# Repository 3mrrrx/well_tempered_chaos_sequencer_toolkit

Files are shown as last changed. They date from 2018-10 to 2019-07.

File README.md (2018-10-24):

# introduction: 

the well-tempered chaos tool-kit is a mechanical chaos based musical system that seeks to create an intuitive musical relation to the underlying generic structures of chaos in systems. Chaos is generated by the paths of ball bearings that fall though a modular geometrical structure of pins. Depending on the path of a ball the sequencer triggers a sound events, such as CV, MIDI or OSC.

https://vimeo.com/296761849

By adding a mechanism to endlessly loop the balls over the pins the chaos can be continuously sampled. Through the repeated sampling of the chaos generated by a pin formation a structure can be recognized. In return the sequencer uses this structure to trigger sound events. By changing the geometrical patterns of the pins different sound event structures can be constructed that resemble or approximate musical patterns. 

When the ball loops infinitely the sequencer can become a musical object, that  autonomously expresses musical structures. The idea, that simulates randomness can converge through mechanical computation to different statistical distributions structures (Gaussian, non-Gaussian, Boltzmann etc.), is used to express well-tempered chaotic musical events. 

# how to run:

for creating the geometry:

1. download and install OpenSCAD
www.openscad.org/

2. run the script to create the STL models

for preparing the arudino:

1. download ans install the Arduino-IDE
https://www.arduino.cc/

# project

The full project description and build  instruction can be found on "hackaday.io" project:
https://hackaday.io/project/161589-the-well-tempered-chaos-sequencer

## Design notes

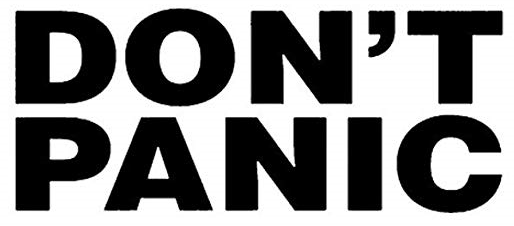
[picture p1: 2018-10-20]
simulation/case_1/dont_apnic.png

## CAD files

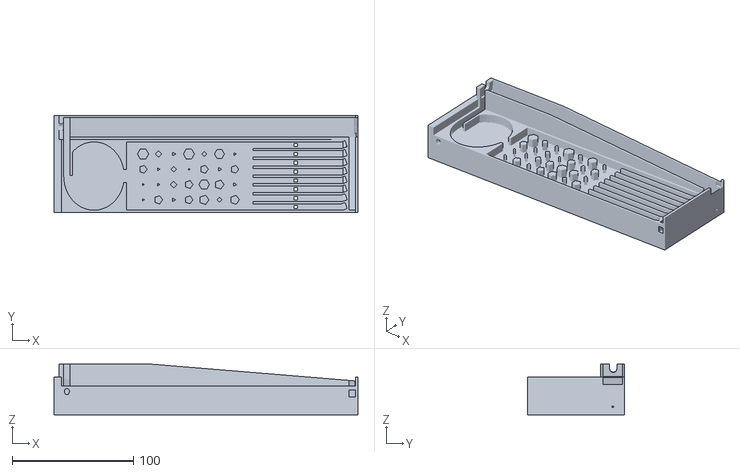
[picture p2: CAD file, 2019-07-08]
geometry/version_4/version4 _BETTER.stl
250.8 x 80.3 x 41.7

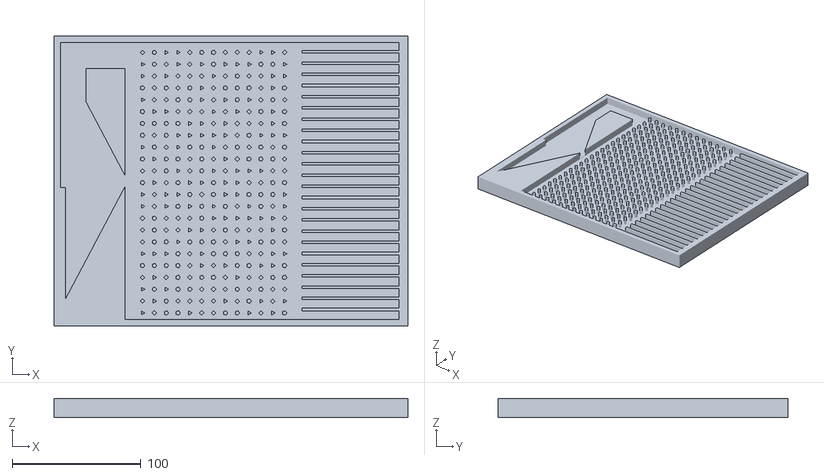
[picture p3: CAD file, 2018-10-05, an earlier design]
geometry/version_1/version_1.1.stl
275.0 x 225.0 x 15.0

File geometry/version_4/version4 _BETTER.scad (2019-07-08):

// well-tempered chaos sequencer board version 3.0
// 5/8/2018   By: 3mrrrx
// GNU GPLv3
// all values are in [mm]


////////////////////////////////////////////
// include functions
////////////////////////////////////////////

include <functions.scad>

////////////////////////////////////////////
// global variables
////////////////////////////////////////////

// tolerance plus ball raduis 
tol = 0.4; //0.24
Ball_raduis = 2.25 + tol;

//thinkness of each of the wall
wall_thinkness = 2 ;

// bottom floor thinknes goes in -z
floor_thinkess = 9.5 + 5;

// board dimenstion 
size_x = 235.55; //240-3.7-1+0.25;
size_y = 60.4;
size_z = Ball_raduis*3.5;

// bin size parameters
cascades_lengths = 115 * size_x/350;
spacing_factor = 1; // factor to multiply to bin width  

// bin end break paramter 
break_factor = 1;  // fraction of bin length 
break_angel  = 20; // angel of bread degs


// fann funnel parameters
funnel_size = 50 ; // lentgh of funnel
funnel_resulition = 50; // funnel cirular resolution
inlet_factor = 2;   // 
$fn = 10;

// fan dimensions
fan_x = 72;
fan_y = 40;
fan_z = 40;
factor_fan = 0.5; // position of fan as a fraction of 


// return channel parameters
channel_width = (Ball_raduis+wall_thinkness)*2;
channel_mid = wall_thinkness;

// motor Size
motor_r = 20+1  +tol;
motor_l = 110;


// debug
shift_factor = 0.1;
debug_eliv = 0;


////////////////////////////////////////////
// geomerty
////////////////////////////////////////////

// board
difference(){

    ////////////////////////////////
    //  summ to peripheres
    ////////////////////////////////
    union(){
            
    ////////////////////////////////
    //  mian board
    ////////////////////////////////
    difference(){

    // bounding box
    scale([size_x,size_y,size_z]) 
    cube(1);
    
    // horizontal tube
    shift_bottom_c = 0;
    length_bottom  = channel_width/2;
    color([0,0,1]) // blue
    translate([0+channel_width/2,size_y/2,size_z/2+debug_eliv*3]) 
    scale([channel_width/2-wall_thinkness*1.3,1,size_z/2-wall_thinkness])
    rotate(a = 90, v = [1, 0, 0]){
        cylinder( h = size_y/2+channel_width/2, r = 1, center = false, $fn=25);};   
    
    ////////////////////////////////
    //  create funnels
    ////////////////////////////////
    funnel(funnel_size,wall_thinkness,size_x,size_y,size_z,funnel_resulition);
    
    ////////////////////////////////
    // bottom box
    ////////////////////////////////
    translate([funnel_size+wall_thinkness*2,wall_thinkness,wall_thinkness])
    scale([size_x-funnel_size-wall_thinkness*2 - cascades_lengths,size_y-wall_thinkness*2,size_z])
        cube(1);
        
    ////////////////////////////////
    // wind tunnel tubing       
    ////////////////////////////////
    
    create_spiral_tubeing(Ball_raduis,wall_thinkness,size_x,size_y,size_z,channel_width,debug_eliv);
        
    ////////////////////////////////
    // create bins
    ////////////////////////////////
    
    Cascades (wall_thinkness,channel_size,cascades_lengths,break_factor,break_angel,size_x,size_y,size_z,Ball_raduis);

    ////////////////////////////////
    // sensor holes
    ////////////////////////////////
        
    // CNY70 heads                
    pin_heads (wall_thinkness,channel_size,cascades_lengths,break_factor,break_angel,size_x,size_y,size_z,Ball_raduis, size = 2.7, scale_x=1);

//    // doubleholes jumper cable bin heads
//    translate([0,1.1,0])
//        pin_heads (wall_thinkness,channel_size,cascades_lengths,break_factor,break_angel,size_x,size_y,size_z,Ball_raduis, size = 1.4, scale_x=1);
//    
//    translate([0,-1.1,0])
//        pin_heads (wall_thinkness,channel_size,        cascades_lengths,break_factor,break_angel,size_x,size_y,size_z,Ball_raduis, size = 1.4, scale_x=1);                  


    ////////////////////////////////
    // plexy glass holder
    ////////////////////////////////
    
    // scaling fixed
    translate([40*size_x/235.55,0,0])
        pin_heads (wall_thinkness,channel_size,cascades_lengths,break_factor,break_angel,size_x,size_y,1,Ball_raduis, size = [7.7,7.7,1.7], scale_x=1);   
                                 
    }

    ////////////////////////////////
    // plexy glass holder
    ////////////////////////////////

//    // bottom    
//    translate([size_x+channel_width-wall_thinkness,-channel_width,0]) 
//    scale([wall_thinkness,wall_thinkness*4+Ball_raduis*8 + size_y,size_z+wall_thinkness+Ball_raduis*2]) 
//        cube(1);
//
//    // top
//    translate([-wall_thinkness*3,-channel_width,-floor_thinkess]) 
//    scale([wall_thinkness*3,wall_thinkness*4+Ball_raduis*8 + size_y,size_z+wall_thinkness+Ball_raduis*2+floor_thinkess])
//        cube(1);
    
    
    // bottom    
    translate([size_x+channel_width-wall_thinkness,0,0]) 
    scale([wall_thinkness,wall_thinkness*4+Ball_raduis*8 + size_y-channel_width,size_z+wall_thinkness+Ball_raduis*2]) 
        cube(1);

    // top
    translate([-wall_thinkness*3,0,-floor_thinkess]) 
    scale([wall_thinkness*3,wall_thinkness*4+Ball_raduis*8 + size_y-channel_width,size_z+wall_thinkness+Ball_raduis*2+floor_thinkess])
        cube(1);
    
    ////////////////////////////////
    // create pins
    ////////////////////////////////    
    
    factor_pins = 1.0;
    // random vector for pin shape resolution 
    random_vec = rands(1,5,50000,9);
    i = 0;
    
    for (x = [62.5+5:Ball_raduis*4+2:223/350*size_x] )
    for (y = [wall_thinkness+Ball_raduis*4-2:Ball_raduis*4*factor_pins+2:size_y-wall_thinkness-Ball_raduis*2]){
        
        i = x*y; // generate index for random vector
        randum_pillar(x,y,random_vec[i] ,size_z,floor(random_vec[i]+2));
    
    }
    

    ////////////////////////////////
    // create channels
    ////////////////////////////////    
    
    channel_size = Ball_raduis*2*spacing_factor;

    // return tube
    difference(){
        
        // create wind channel box
        difference(){

        // side spiral box 
        color([1,1,1]) // green        
            side_spiral_box(Ball_raduis,channel_width,size_x,size_y,size_z,debug_eliv);
        
        // wind channel tubing 
//        color([1,0,0]) // red
//            create_spiral_tubeing(Ball_raduis,wall_thinkness,size_x,size_y,size_z,channel_width,debug_eliv);
            
//       color([1,0,0]) // red
//            
                    rotate(12, [1,0,0])
        translate([0,-1.7,-Ball_raduis*3.5])

            create_spiral_tubeing(Ball_raduis,wall_thinkness,size_x,size_y+3,size_z,channel_width,debug_eliv);
            
            
            
                  color([1,0,0]) // red
            
//                    rotate(12, [1,0,0])
        translate([0,wall_thinkness,-Ball_raduis*3.5])

            create_spiral_tubeing(Ball_raduis,wall_thinkness,size_x,size_y-wall_thinkness,size_z+10,channel_width,debug_eliv); 
            
            
        }
        
        // CUTE THE BIN CHANNELS FORM THE BAORDES OF THE
        color([1,0,0]) // red
            Cascades (wall_thinkness,channel_size,cascades_lengths,break_factor,break_angel,size_x,size_y,size_z,Ball_raduis);
    }

        // side wind box 
       // color([1,0,1]) // green
      //      side_wind_box_fan(Ball_raduis,channel_width,size_x,size_y,size_z,fan_x, fan_y, fan_z, factor_fan, debug_eliv);

    ////////////////////////////////
    // floor
    //////////////////////////////// 
    difference() {
        
        //////////////////////////////// 
        // FLOOR BOX
        //////////////////////////////// 
        
        union(){
            
            // UNDER THE BOARD
//            translate([0,-channel_width,-floor_thinkess]) 
//            scale([size_x+channel_width,size_y+   channel_width*2+Ball_raduis*3+2.5,floor_thinkess]) 
//                cube(1);   
            
            translate([0,0,-floor_thinkess]) 
            scale([size_x+channel_width,size_y+   channel_width*1+Ball_raduis*3+2.5,floor_thinkess]) 
                cube(1);   

            // under the fan
         //   translate([size_x*factor_fan-fan_x*0.5,-fan_y,-floor_thinkess]) 
        //    scale([fan_x*2,fan_y,floor_thinkess]) 
        //        cube(1);   
        }

        //////////////////////////////// 
        // FLOOR CUTS
        //////////////////////////////// 


        // FALL TO PIT CUT
        translate([0,0,-32]) 
            pin_heads(wall_thinkness,channel_size,cascades_lengths,break_factor,break_angel,size_x,size_y,floor_thinkess,Ball_raduis, size = [8,8,floor_thinkess], scale_x=1);
    
        
         // JUMPER CABLE PATHS VERTICAL
        translate([-32,0,-floor_thinkess/2]) 
            pin_heads(wall_thinkness,channel_size,cascades_lengths,break_factor,break_angel,size_x,size_y,floor_thinkess,Ball_raduis, size = [3.4,3.4,3.4], scale_x=size_x/6);
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

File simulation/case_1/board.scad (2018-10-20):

// well-tempered chaos sequencer board version 1.0 reworked
// 5/8/2018   By: 3mrrrx
// GNU GPLv3


//////// modules
module  random_pillar(x=1, y=1,height=20, raduis = 2, resulation = 6, b=0) { 
    
    translate([x,y,height/2]) 
    
            rotate(b,[0,0,1])

    cylinder($fn = resulation, $fa = 12, $fs = 2, h = height, r1 = raduis, r2 = raduis, center = true);
    
    }

//////// variables
// size
size_x = 275;
size_y = 225;
size_z = 15;

// wall thikness    
wall = 5;

// bearing ball raduis
r_ball = 2.25;
    
// toleranz
tol = 0.2;    
    
//////// model
//// Board
//difference(){

//// bounding_box
//scale([size_x,size_y,size_z]) cube(1);
//
////  funnel for holding the balls hold
//$fn =3; 
//translate([wall*5,size_y/2,size_z+wall-1.5]) scale([size_x/6,size_y/1.5,size_z]) sphere(radius = 1);
    

//// return tube
//translate([wall+5,size_y-wall*5,size_z/2]) scale([size_x*0.2,wall*4,size_z/2]) cube(1);
//    
//translate([wall+5,size_y-wall-size_y/2,size_z/2]) scale([wall*2,size_y/2,size_z/2]) cube(1);    

// bottem box
//translate([size_x*0.2,wall,size_z/2]) scale([size_x*0.775,size_y-wall*2,size_z]) cube(1);

    
//}


//// create pins
// random seed

wid=58; 
logox = 514; 
logoy = 226; 

translate([size_x*0.7,0,0]) 

rotate(90,[0,0,1])

scale([1.6,1.6,size_z])

difference(){ 
    
    translate([wid/4,wid/4,1]) 
        scale([wid/logox*2,wid/logoy,1/255]) 
             surface("C:/Users/hasan/Desktop/dont_apnic.png",invert=true); 
    cube([wid*2.5,wid*1.5,1]); 


} 


//// create bins
//wall_bin = 2;
//bin_step = wall_bin*2+r_ball*2+tol;
//        
// for (y = [wall+bin_step-wall_bin:bin_step:size_y-wall] )
// {
//translate([size_x*0.7,y,0]) scale([size_x*0.3,wall_bin,size_z]) cube();
// }
 

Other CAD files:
geometry/version_1/board_1.0.scad
geometry/version_1/board_1.1.scad
geometry/version_2/version_2.scad
geometry/version_3.5/fan_functions.scad
geometry/version_3.5/functions.scad
geometry/version_3.5/spiral.scad
geometry/version_3.5/spiral_functions.scad
geometry/version_3.5/version4.scad
geometry/version_3/functions.scad
geometry/version_3/spiral.scad
geometry/version_3/version_3.0.scad

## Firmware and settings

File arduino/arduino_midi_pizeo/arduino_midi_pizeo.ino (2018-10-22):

// well-tempered chaos sequencer board version 2.0
// Pizeo to MIDI
// 5/8/2018   By: 3mrrrx
// GNU GPLv3
// all values are in [mm]

#include <MIDI.h>


// will store last time LED was updated
unsigned long previousMillis = 0;   

// interval at which to blink (milliseconds)     
const long interval = 5000;     // in (milliseconds)        

// threshold value for each of the sensor
const int threshold[] = {
  30, 30, 30, 30, 30, 30, 30, 30 
};

// array for holding sesnor values
int myInts[8];

// check if note is played
int note_on[]= {
  0, 0, 0, 0, 0, 0, 0, 0 
};

// intger for holding velocity for midi send 
int vel = 0 ;

 // Created and binds the MIDI interface to the default hardware Serial port
MIDI_CREATE_DEFAULT_INSTANCE();

// debug = 1;

void setup() {

     MIDI.begin();

}

void loop() {

  //unsigned long currentMillis = millis();

  //if (currentMillis - previousMillis >= interval) {
    // save the last time since last sesnor reading
  //  previousMillis = currentMillis;

   for (int i=0; i < 8; i++){
    myInts[i] = analogRead(i);

    
//    Serial.print(myInts[i]);      //the first variable for plotting
//    if(i != 7){
//    Serial.print(","); 
//    }
//    else
//    {
//    Serial.println(" "); 
//    }


      if (myInts[i] >= threshold[i]) {
        //if (note_on[i] == 0) { 
          
          // mal Pizeo value to MIDI velocity
          // vel = map(piezoReading, 0, 1023, 40, 127);
          
          MIDI.sendNoteOn(42+i, 110, 1);
          note_on[i] = 1 ;
          
          //} else {

          delay(20);
          
          MIDI.sendNoteOff(42+i, 110, 1);
          note_on[i] = 0 ;
          
        }
      }
    }
//}
//}

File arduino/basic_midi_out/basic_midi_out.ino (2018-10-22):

// well-tempered chaos sequencer board version 2.0
// Pizeo to MIDI
// 5/8/2018   By: 3mrrrx
// GNU GPLv3
// all values are in [mm]

#include <MIDI.h>


const int piezo = A0; // analog pin 0 is connected to the Pizeo 
const int threshold = 100;  // threshold value to filter 


int piezoReading = 0;      // variable to store the value read from the piezo 
int vel = 0 ;              // variable to store the velocity value

 // Created and binds the MIDI interface to the default hardware Serial port
 MIDI_CREATE_DEFAULT_INSTANCE();

 
 // this function is called on arduino start
 void setup()
 {
     MIDI.begin();
 }

 void loop()
 {

     // Send note on 42 with velocity 127 on channel 1
     MIDI.sendNoteOn(42, 127, 1);

     // wait for 500 ms
      delay(100);

     // Send note off 42 with velocity 127 on channel 1
     MIDI.sendNoteOff(42, 127, 1);

     
     // wait for 500 ms
      delay(100);

  
}



 
 

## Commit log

2018-10-05 ´first commit
    ´first commit
    [board_1.0.scad, board_1.1.scad, version_1.1.stl]
2018-10-08 updated version_2.0 and version_3.0
    [functions.scad, spiral.scad, version_2.scad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]
2018-10-19 UPDATED VERSION 4
    [fan_functions.scad, functions.scad, spiral.scad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]
2018-10-19 ADDED SPRIAL ROATION PARAMETER
    [spiral.scad]
2018-10-20 UPDATED PARAMTERS
    [fan_functions.scad, functions.scad, spiral.scad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]
2018-10-20 added simulation case
    [board.scad]
2018-10-20 spelling mistake
    [version4.scad]
2018-10-21 arduino
    added arduino code
    [spiral_functions.scad, version4.scad]
2019-07-08 created a better version of 4
    [version4 _BETTER.scad, version4 _BETTER.stl]
